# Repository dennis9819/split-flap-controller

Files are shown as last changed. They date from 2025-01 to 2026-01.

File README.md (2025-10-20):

# 3D Printable split flap display

Welcome to **split-flap-controller**, the firmware + hardware design for driving a modular, scalable split-flap display system.
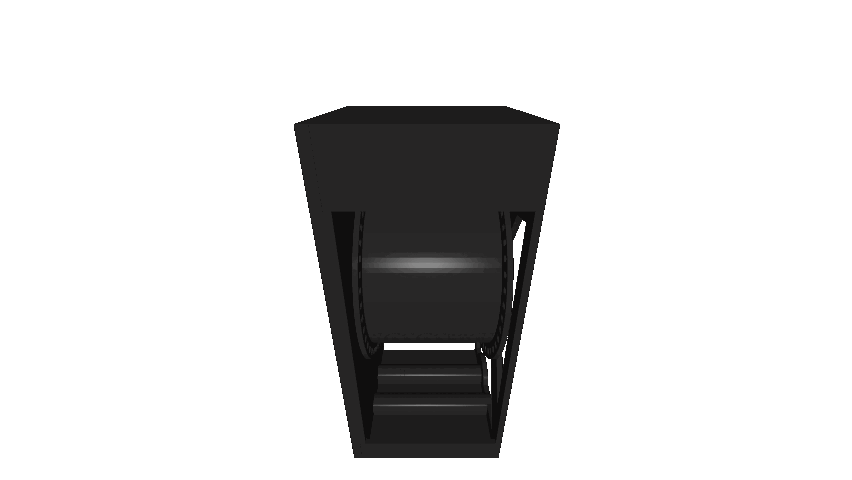
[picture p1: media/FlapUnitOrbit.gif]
Orbit View of Flap Unit


Development of this project began in 2024 with the goal of creating a robust, DIY split-flap display that anyone can build and customize themselves. Inspired by the iconic Frankfurt Airport display, this project aims to recreate the nostalgic mechanical aesthetic and characteristic flipping sound that made those displays so memorable.

__Ongoing Project! This repository is not final.__

## Project goals
- **Modularity** – Each flap module is independent and addressable, allowing for scalable display sizes.  
- **DIY-Friendly Design** – Open schematics, PCBs, and firmware make it accessible for makers and hobbyists.  
- **Robust Firmware** – Written in C, with features like error handling, EEPROM-stored calibration, and motor homing logic.  
- **Authentic Aesthetic** – Recreates the distinctive motion and sound of traditional airport-style displays.  
- **Modern Communication** – Supports RS-485 half-duplex at 57600 baud with WebSocket integration for control from a host system.  
- **Open for Extension** – Designed to support other MCUs, motor drivers, or mechanical formats.

## Features

### Hardware
- SMD-based controller board (Atmega8 MCU)  
- Modular RS-485 communication chain 
- Integrated motor driver and position sensor handling
- Modules connect to a single backplane
- Hall-effect sensor homing
- Robust error handling
  - detects homing faults, stuck drums, overcurrent and bus errors
  - activates a failSafe condition on critical fault
  - can be reset via RS485 in most conditions
  - checks validity of each packet via checksum

### Firmware
- Lightweight communication protocol with checksum and addressing  
- Fault detection (homing failure, overcurrent, invalid position)  
- Persistent settings stored in EEPROM  
- CRC check of each message

### Software
- WebSocket-based control server  
- Modular architecture for future GUI or API integrations  
- Easily portable to other platforms and MCUs
- Nginx Webserver allows you to controll the display with your smartphone
- very fast and written in plan c. I'm using libjson and libws for JSON handling and the WebSocket server

## CAD
This display is designed in **Fusion360**. All schematics and boards are designed in **KiCAD 9**.

Most parts can be 3d printed. The modular backpanel needs to be fabricated from sheetmetal. You can use suppliers like JLCPCB for manufacturing or design a different 3d printable solution.

If you want to generate custom flaps, you can find my flap generator here: [split-flap-generator](https://github.com/dennis9819/split-flap-generator)

## License

This project is open source and available under the [AGPL-3.0 License](LICENSE).

## Documentation
- [SFBus Protocol](software/pc_client/doc/sfbus-proto.md)
- [Websockets Protocol](software/pc_client/doc/api-doc.md)
- [BOM](cad/BOM_FlapUnit.md)
- Build guide wil follow soon!

## Power Consumption
Each Module pulls arround 110mA. This is roughly 1.4W of power. 
This can be reduced by turning off the motors in idle. 

---
## Credits
This is a 3D printable, expandable split flap display based on the original design of [David Königsmann](https://github.com/davidkingsman/split-flap).
This version uses his drum and flap design but completly redesigns the rest of the system.

The firmware as well as the Server is completly rewritten from scratch.

Feel free to checkout his more affordable and diy friendly design.

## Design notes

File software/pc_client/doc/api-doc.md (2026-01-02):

# Websockets Interface documentation
All requests and responses are sent as json objects.

## Request
Every request must conatin at least one value: `command`
```
{
   "command": "<command>"
}	
```
### Device manager commands

#### Save config `dm_save`
Saves config to ./flapconfig.json.

Request:
```
{
   "command": "dm_load"
}	
```
Response:
```
{
   "ack": true
}	
```
#### Load config `dm_load`
Loads config from ./flapconfig.json.

Request:
```
{
   "command": "dm_load"
}	
```
Response:
```
{
   "ack": true
}	
```
#### Dump config `dm_dump`
Dumps current config to socket.

Request:
```
{
   "command": "dm_dump"
}	
```
Response:
```
{
   "devices_all": <registered device count>
   "devices_online": <online device count>,
   "devices": <array of all devices>,
   "map": <2D array of device locations>
}	
```

#### Describe single device `dm_describe`
Gets all information for specified device id.

Request:
```
{
   "command": "dm_describe",
   "id": <device id>
}	
```
Response:
```
{
   ...
}	
```
#### Register new device `dm_register`
Register device, assign new id and assign a location.
```
{
   "command": "dm_describe",
   "address": <device bus address>,
   "x": <x position on screen>,
   "y": <y position on screen>,
}	
```
Response:
```
{
   "id": <assigned device id>
}	
```

#### Remove device from config `dm_remove`
Removes device from config and frees location in screen

Request:
```
{
   "command": "dm_remove",
   "id": <device id>
}	
```
Response:
```
{
   "ack": true
}	
```

#### Remove device from config `dm_refresh`
Refresh device config

Request:
```
{
   "command": "dm_refresh"
}	
```
Response:
```
{
   "devices_online": <online device count>
}	
```

#### Print string `dm_print`
Print string at position (x,y)

Request:
```
{
   "command": "dm_describe",
   "string": <string to display>,
   "mode": <int: 0=full rotation/1=direct/2=sync>,
   "x": <int: x position on screen>,
   "y": <int: y position on screen>
}	
```
Response:
```
{
   "ack": true
}	
```

#### Display flap number `dm_print_single`
Print string at position (x,y)

Request:
```
{
   "command": "dm_print_single",
   "flap": <int: flap to display>,
   "full": <boolean: full rotation of drum/recalibration>,
   "x": <int: x position on screen>,
   "y": <int: y position on screen>
}	
```
Response:
```
{
   "ack": true
}	
```

#### Display clear `dm_clear`
Clears all flaps.

Request:
```
{
   "command": "dm_clear"
}	
```
Response:
```
{
   "ack": true
}	
```

### Device raw commands

#### Ping module `dr_ping`
Checks if a module reponds on the given address.

Request:
```
{
   "command": "dr_ping",
   "address": <address>
}	
```
Response:
```
{
   "success": <boolean: if device reponded 'true', else 'false'>
}	
```

#### Set module address `dr_setaddress`
Changes the hardware address of an module.

Request:
```
{
   "command": "dr_setaddress",
   "address": <address>,
   "newaddress": <new address>
}	
```
Response:
```
{
   "success": <boolean: if success 'true', else 'false'>
}	
```

#### Set module offset calibration `dr_setcalibration`
Sets the offset calibration for an module.

Request:
```
{
   "command": "dr_setcalibration",
   "address": <address>,
   "calibration": <calibration value (default: 1800)>
}	
```
Response:
```
{
   "success": <boolean: if success 'true', else 'false'>
}	
```

#### Reset module `dr_reset`
Resets the controller of an module

Request:
```
{
   "command": "dr_reset",
   "address": <address>
}	
```
Response:
```
{
   "ack": true
}	
```

#### Display flap `dr_display`
Sets the module to the specified flap directly or with recalibration.

Request:
```
{
   "command": "dr_display",
   "address": <address>,
   "flap": <flap-number>,
   ("full": <boolean: full rotation of drum/recalibration>)

}	
```
Response:
```
{
   "ack": true
}	
```

#### Power module on/off `dr_power`
Sets the power-state for the motor of the given module.

Request:
```
{
   "command": "dr_power",
   "address": <address>,
   "power": <boolean: power on>

}	
```
Response:
```
{
   "ack": true
}	
```

## Responses
### Error:
```
{
   "error": "<error name>",
   "detail": "<more detailed error message>"
}	
```
The following responses are valid:
- `parsing error`: the json request is malformated and cannot be parsed
- `format error`: the json object is missing required fields. Check details for more information.
- `internal error`: an internal error occured. This should not happen. Chaeck server logs.

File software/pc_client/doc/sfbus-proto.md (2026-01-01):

# SplitflapBus protocol
## Terminology
* *main controller interface*: RS485 interface, connected to the mangment pc. Serves as bus master.
* *node*: Participant on bus. Can be a controller interface or an flap controller.
* *flap controller*: Microcontroller located in each flap module that processes requests and drives motor.

## Protocol implementation
The SF-Bus is an RS485 based protocol. It has a singular master node and up to 32 client *nodes* per interface.  It can address up to 65536 *devices*.

The communication is always initiated by the *main controller interface*, serving as the bus *master*.
The start of a new communication is signaled by sending the start byte `0x2B` to the bus, followed by the protocol version (8-bit) and frame length (8-Bit). Each connected *node* now captures the entire packet, even if the adress does not match its own. This reduces the risk of the *node* falsely identifying payload data as a start byte if it contains the value `0x2B`.

After the transmission of the payload length, the receiver *node* counts the remaining packages and terminates the transmission at 0 bytes remaining. The data is written to a buffer for further processing.

In protocol version 1.0, the receiving *node* expects the last byte to be `0x24`. If this is not the case, the transmission is marked as invalid and will not be processed further. The receiving *node* will not send any response.

In protocol version 2.0, the checksum of the payload is verified. If it does not match the payload, the transmission is marked as invalid and will not be processed further. The receiving *node* will not send any response.
No stop-byte is expected. Version 2.0 also requires a timeout-check in the receiving function. This allows the bus to support hot-plugging, to cancel incomplete or invalid packages and reliably detect the start of a new transmission.

The communication is typically unidirectional. Lost transmissions are not detectable. The *flap controller* NEVER initiates a communication to the *main controller interface*. *node* to *master* communication only occures in response to specific commands. This is specified in the command / payload documentation.

## Packet format (2.0)
```
+---------------------------------+----------------------------------------+
| Header                          | Frame                                  |
+------------+-----------+--------+----------+-----------------+-----------+
| Start-Byte | Protocol- | Frame- | Receiver | Payload         | Checksum  |
|            | Version   | Length | Address  |                 |           |
| 0x2B       | 0x01      | 1 byte | 2 bytes  | framelength - 4 | 2 bytes   |
+------------+-----------+--------+----------+-----------------+-----------+
 The frame length includes the 16-bit address and 16 bit checksum.
 Therefor, the payload is framelegth - 4.

 Checksum is based on MODBUS CRC algorithm. Check implementation in sfbus.c
 Checksum is only created for the payload, not the entire frame or packet.
```

More infromation regarding the crc algorithm: https://ctlsys.com/support/how_to_compute_the_modbus_rtu_message_crc/

## Payload format (Protocol Version 1.0 + 2.0)
The first byte of the payload is the command. This tells the controller
what to do or what data to expect next.

```
+----------+----------------+
| Command  | Payload        |
| Byte     |                |
| 1 Byte   | framelegth - 4 |
+----------+----------------+
```

### Ping
Check if a module is present under this device id
- Payload: `0xFE`
- Expected response: `0xFF`

### Reset
Resets the device controller. Should be done after address or calibration change.

Can also be done to clear error flags
- Paylad `0x30`
- Expects no response.

### Motor power on
- Paylad `0x21`
- Expects no response.

### Motor power off
- Paylad `0x20`
- Expects no response.

### Display flap
- Paylad `0x10 <1 byte: flap id>`
- Expects no response.

### Display flap with full rotation
- Paylad `0x11 <1 byte: flap id>`
- Expects no response.

### Read EEPROM
Read address and calibration configuration from internal non-volatile memory.
- Payload `0xF0`
- Response is `0xAA` followed by content of EEPROM (5 bytes). See mapping below.

### Write EEPROM
Write address and calibration configuration to internal non-volatile memory.
- Payload `0xF1 <5 bytes of eeprom content>`
- Response is `0xAA` followed by new content of EEPROM (5 bytes). See mapping below.

### Get controller status
- Payload `0xF8`
- Response is 7 bytes long.
```
+--------+------------+------------+
| Byte 0 | Byte 1 - 2 | Byte 3 - 6 |
| 8-Bit  | 16-Bit     | 32-Bit     |
| Status | Voltage    | Rotations  |
+--------+------------+------------+
  |         |            |
  |         |            +-> uint32 counter of total rotations
  |         |
  |         +-> uint16 raw ADC readings.
  |             double __voltage = ((double)_voltage / 1024) * 55;
  |
  +->   Bit 0:  delta too big. Sensed position not equal to expected position
        Bit 1:  no home found. Cannot sense home magnet.
        Bit 2:  fuse blown
        Bit 4:  device powered down. Can be changed by sending: 0x21
        Bit 5:  failsafe active. Device failed cirtically and stopped operation.
                can be recovered with reset: 0x30
        Bit 6:  device busy. Device is currently moving to the next flap position

```

### Get controller firmware version
- Payload `0xF9`
- Response is 3 bytes long: `<major> <minor> <patch>`.

## EEPROM format
```
+------------+------------+--------+
| Byte 0 - 1 | Byte 2 - 5 | Byte 6 |
| 16-Bit     | 32-Bit     | 8-Bit  |
| Address    | Rotations  | Okay   |
+------------+------------+--------+
  |             |           |
  |             |           +-> do not change
  |             |
  |             +-> uint32 counter of total rotations
  |
  +-> uint16 device address
```

## Address management
* Address `0x0000` is reserved for new devices. These devices needs a new address before it can be used. Use the `Write EEPROM` method to change it.
* Address `0xFFFF` is reserved for the bus *master* and must never be used by another node. Each *node* to *master* response package must be sent to this address.
* All remaining addresses can be freely assigned.

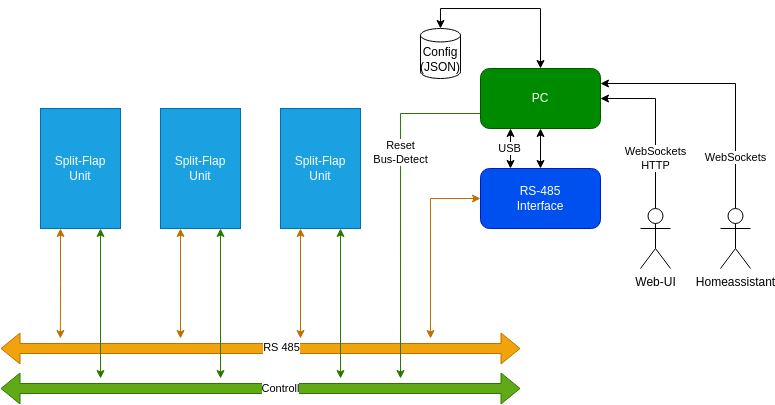
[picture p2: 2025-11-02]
media/SplitFlap-Doc-Overview.drawio.png

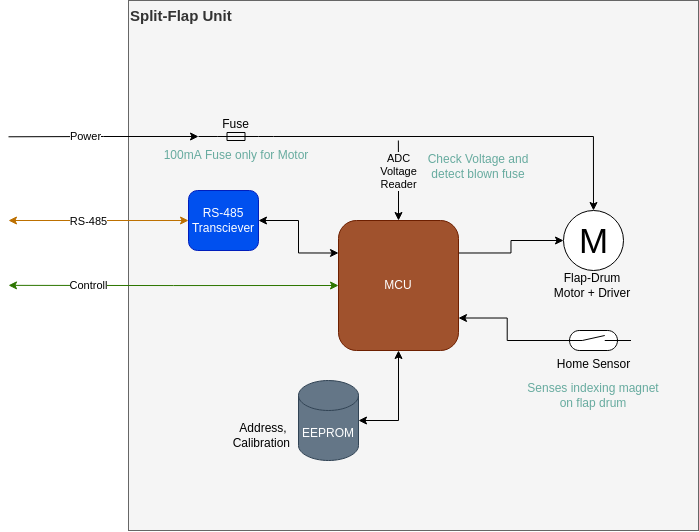
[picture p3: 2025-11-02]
media/SplitFlap-Doc-Module.drawio.png

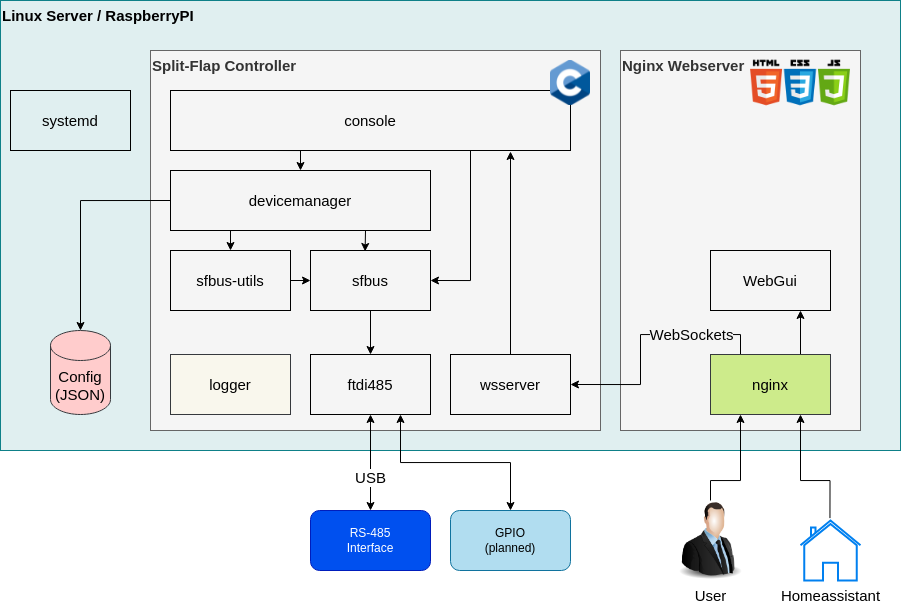
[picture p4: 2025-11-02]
media/SplitFlap-Doc-Controller-SW.drawio.png

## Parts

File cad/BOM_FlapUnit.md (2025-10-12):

# Bill of Material for 1U/2U Flap Unit

## 3D Printed Parts 
| part-number | part | file | amount | notes |
| --- | ---- | ---- | --- | ----- |
| FU-001 | Unit Frame Base | STL Unit/splitflap-unit-base.stl | 1 | common for all units |
| FU-002 | Unit Frame Cover 1U | STL Unit/splitflap-cover-1u.stl  | 1 | only for 1U wide unit|
| FU-003 | Unit Frame Cover 2U | STL Unit/splitflap-cover-2u.stl  | 1 | only for 2U wide unit|
| FU-004 | Unit Drum Core | STL Unit/splitflap-drum-core.stl | 1 | common for all units |
| FU-005 | Unit Drum Core 1U | STL Unit/splitflap-drum-outer-1u.stl | 1 | only for 1U wide unit|
| FU-006 | Unit Drum Core 2U | STL Unit/splitflap-drum-outer-2u.stl | 1 | only for 2U wide unit|
| FU-007 | Flaps | ... | 45 | |
- 49 Individual Parts per module

## Hardware

| part-number | part | amount | notes |
| --- | ---- | --- | ----- |
| FU-011 | Ball Bearing 684ZZ (9 x 4 x 4mm) | 1 | |
| FU-012 | Stepper 28BYJ-48 DC 12V | 1 |  **!! Use 12V Variant. NOT 5V !!**|
| FU-013 | Heat insert M3 x 3mm | 3 | |
| FU-014 | Heat insert M3 x 5mm | 4 | |
| FU-015 | M3x5 Screw DIN 912 | 3 | |
| FU-016 | M3x12 Screw DIN 912 | 2 | |
| FU-017 | M3x8 Screw DIN EN ISO 10642 | 2 | |
| FU-018 | Magnet round d=2mm | 1 | |
- 17 Individual Parts per module

## Electronics
| part-number | part | amount | notes |
| --- | ---- | --- | ----- |
| FU-031 | Module Controller PCB | 1 | |
| FU-032 | ATmega8A-A | 1 | |
| FU-033 | SN75176AP | 1 | |
| FU-034 | ULN2003 | 1 | Can be salvaged from the driver board that usually comes with the stepper motor |
| FU-035 | A1101xLH | 1 | SOT-23W variant! |
| FU-036 | 16,0000-HC49U-S Crystal | 1 |  |
| FU-037 | Capacitor 10u 35V (Radial_D6.3mm_P2.50mm) | 1 |  |
| FU-038 | Capacitor 10u 16V (1206) | 1 |  |
| FU-039 | Capacitor 22p (0805) | 2 |  |
| FU-040 | Capacitor 100n (0805) | 4 |  |
| FU-041 | Fuse 200mA (0805) | 1 |  |
| FU-042 | JST B5B-XH-A | 1 |  |
| FU-043 | Resistor 1k | 1 |  |
| FU-044 | Resistor 10k | 3 |  |
- 20 Individual Parts per module

## Summary:
Parts per module: 76 (mostly 3d printed)

# Bill of Material for 4Unit Backplane

## 3D Printed Parts 
| part-number | part | file | amount | notes |
| --- | ---- | ---- | --- | ----- |
| FP-001 | Upper Slot | STL Slot/splitflap-slot-upper.stl | 1 |  |
| FP-002 | Lower Slot | STL Slot/splitflap-slot-lower.stl | 1 |  |
- 2 Individual Parts per module

## Sheet metal
| part-number | part | file | amount | notes |
| --- | ---- | ---- | --- | ----- |
| FP-003 | Backplane | Sheet Metal/sheet-metal-backplate.dxf | 1 |  |
- 1 Individual Parts per module

## Hardware
| part-number | part | amount | notes |
| --- | ---- | --- | ----- |
| FP-011 | Heat insert M4 x 5mm | 4 | |
| FP-012 | Heat insert M3 x 5mm | 4 | |
| FP-013 | M3x5 Screw DIN 912 | 8 | |
| FP-014 | M4x10 Screw DIN 912 | 4 | |
| FP-015 | M3x5 Standoff | 8 | |
| FP-016 | M3 Nut | 4 | |
- 32 Individual Parts per module

## Electronics
| part-number | part | amount | notes |
| --- | ---- | --- | ----- |
| FP-031 | Backplane PCB | 1 | |
| FP-032 | PhoenixContact_MSTBA_2,5_2-G-5,08 | 2 | |
| FP-033 | Phoenix_MSTB:PhoenixContact_MSTBA_2,5_3-G-5,08 | 4 | |
| FP-034 | L7805 | 1 |  |
| FP-035 | 74AHCT1G125 | 1 | |
| FP-036 | 2x08 Edge Connector | 4 |  |
- 13 Individual Parts per module

## Summary:
Parts per assembly: 48 

# Bill of Material for Backplane connection bracket
## Sheet metal
| part-number | part | file | amount | notes |
| --- | ---- | ---- | --- | ----- |
| FC-001 | Bracket | sheet-metal-connector-middle.dxf | 1 |  |
- 1 Individual Parts per module

## Hardware
| part-number | part | amount | notes |
| --- | ---- | --- | ----- |
| FC-011 | M4x10 | 8 | |
| FC-012 | M4 Nut | 8 | |
- 16 Individual Parts per module

## Summary:
Parts per assembly: 17 

# Parts for full display (12x3)
- Display Units: 36 (2736 Parts)
- Backplane Units: 9 (432 Parts)
- Backplane Connectors: 12 (204 Parts)
- Sum: 3372 Individual Parts

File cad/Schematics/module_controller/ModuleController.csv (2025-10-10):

Reference | Value | Footprint | Datasheet | Qty | DNP
C1 | 10u 35V | Capacitor_THT:CP_Radial_D6.3mm_P2.50mm | ~ | 1
C2 | 10u 16V | Capacitor_SMD:C_1206_3216Metric | ~ | 1
C3,C4 | 22p | Capacitor_SMD:C_0805_2012Metric | ~ | 2
C5,C6,C7,C8 | 100n | Capacitor_SMD:C_0805_2012Metric | ~ | 4
F1 | RXEF010 | Capacitor_THT:C_Disc_D7.5mm_W2.5mm_P5.00mm | ~ | 1
H1,H2,H3 | MountingHole | MountingHole:MountingHole_3.2mm_M3 | ~ | 3
J1 | JST B5B-XH-A | Connector_JST:JST_XH_B5B-XH-A_1x05_P2.50mm_Vertical | ~ | 1
J6 | 2x08 Edge Connector | Dennis:Card Edge 16 power | ~ | 1
R1,R2,R4 | 10k | Resistor_SMD:R_0805_2012Metric | ~ | 3
R3 | 1k | Resistor_SMD:R_0805_2012Metric | ~ | 1
U1 | ULN2003 | Package_DIP:DIP-16_W7.62mm | http://www.ti.com/lit/ds/symlink/uln2003a.pdf | 1
U2 | A1101 | Dennis:UA A1101 | https://www.allegromicro.com/-/media/files/datasheets/a110x-datasheet.ashx | 1
U3 | SN75176AP | Package_DIP:DIP-8_W7.62mm | http://www.ti.com/lit/ds/symlink/sn75176a.pdf | 1
U4 | ATmega8A-A | Package_QFP:TQFP-32_7x7mm_P0.8mm | http://ww1.microchip.com/downloads/en/DeviceDoc/Microchip%208bit%20mcu%20AVR%20ATmega8A%20data%20sheet%2040001974A.pdf | 1
Y1 | 16,0000-HC49U-S | Crystal:Crystal_HC49-U_Vertical | ~ | 1

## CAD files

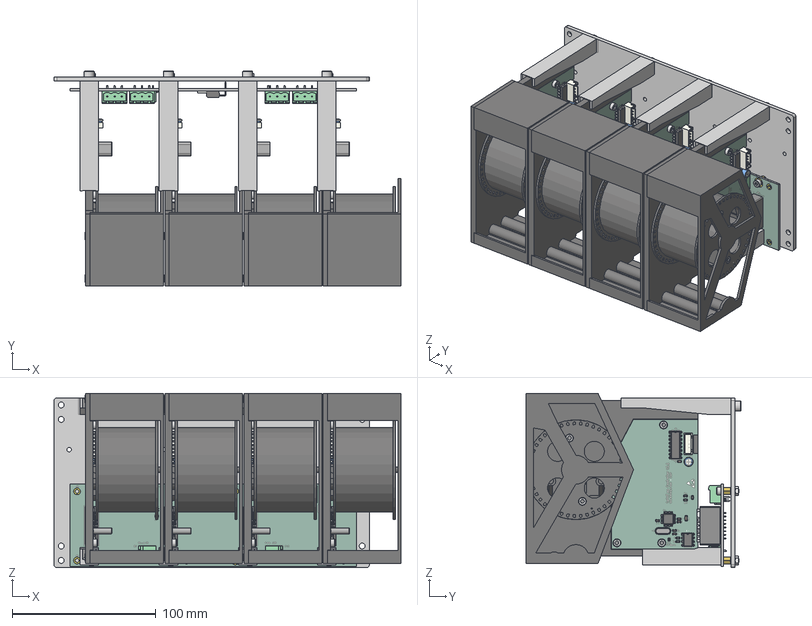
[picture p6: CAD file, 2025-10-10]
cad/STEP/SplitFlap Assembly.step
241.0 x 149.2 x 121.0 mm
Frame x 4
Cover 1U x 4
BigRotor x 4
MiniRotor x 4
DIN 912 - M3 x 0.5 x 8 Steel 4.6 Plain x 12
C_1206_3216Metric x 4
C_0805_2012Metric x 24
R_0805_2012Metric x 16
Crystal_HC49-U_Vertical x 4
TQFP-32_7x7mm_P0.8mm x 4
CP_Radial_D6.3mm_P2.50mm x 4
DIP-16_W7.62mm x 4
SOT-23W x 4
DIP-8_W7.62mm x 4
JST_XH_B5B-XH-A_1x05_P2.50mm_Vertical x 4
Fuse_0805_2012Metric x 4
ModuleController_copper x 4
ModuleController_pad x 4
ModuleController_via x 4
ModuleController_silkscreen x 4
ModuleController_soldermask x 4
ModuleController_PCB x 4
DIN 912 - M3 x 0.5 x 5 Steel 4.6 Plain x 16
DIN EN ISO 10642 - M3 x 8 Steel 8.8 Plain x 8
PhoenixContact_MSTBA_2,5_2-G-5,08_1x02_P5.08mm_Horizontal x 2
Card Edge Slot Connector casing x 4
EDGE_CONN_PIN x 64
PhoenixContact_MSTBA_2,5_3-G-5,08_1x03_P5.08mm_Horizontal x 4
TO-220-3_Horizontal_TabDown
SOT-353_SC-70-5
splitflap-backplane_copper
splitflap-backplane_silkscreen
splitflap-backplane_soldermask
splitflap-backplane_PCB
back-plate
M3_M_TO_F_5MM_STANDOFF x 8
DIN 934 - M3 x 0.5 Steel 6 Plain x 8
F1-B-M4-Heatfit x 4
DIN 912 - M4 x 0.7 x 8 Steel 4.6 Plain x 4

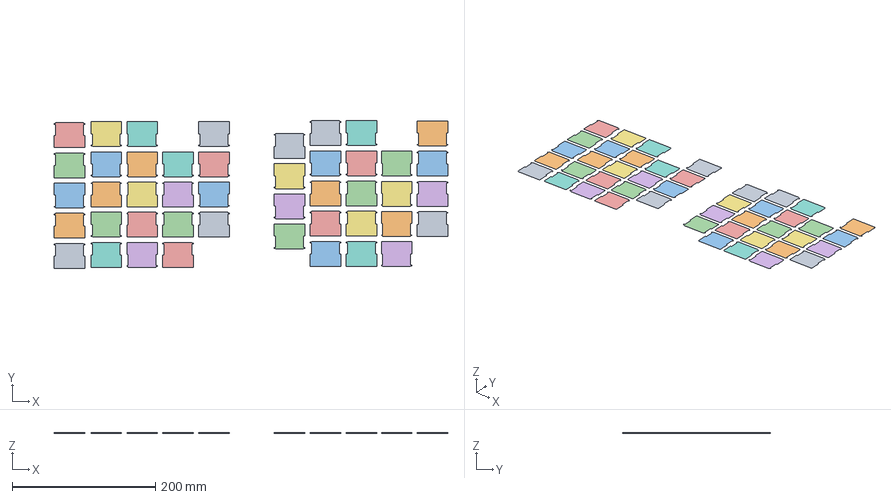
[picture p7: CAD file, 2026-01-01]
cad/Orca/SF_Flaps_V1.3mf
549.9 x 206.2 x 1.00 mm
Flap31.stl
Flap27.stl
Flap28.2.stl
Flap3.stl
Flap15.stl
Flap4.stl
Flap5.stl
Flap25.stl
Flap32.stl
Flap33.stl
Flap29.stl
Flap34.stl
Flap35.stl
Flap30.4.stl
Flap6.stl
Flap37.2.stl
Flap14.4.stl
Flap38.2.stl
Flap39.stl
Flap24.3.stl
Flap40.stl
Flap41.stl
Flap16.stl
Flap42.stl
Flap44.2.stl
Flap23.stl
Flap10.2.stl
Flap19.2.stl
Flap45.2.stl
Flap1.stl
Flap43.stl
Flap7.stl
Flap2.stl
Flap8.stl
Flap9.stl
Flap11.stl
Flap12.stl
Flap13.stl
Flap17.stl
Flap18.stl
Flap36.stl
Flap20.stl
Flap21.stl
Flap22.stl
Flap26.stl

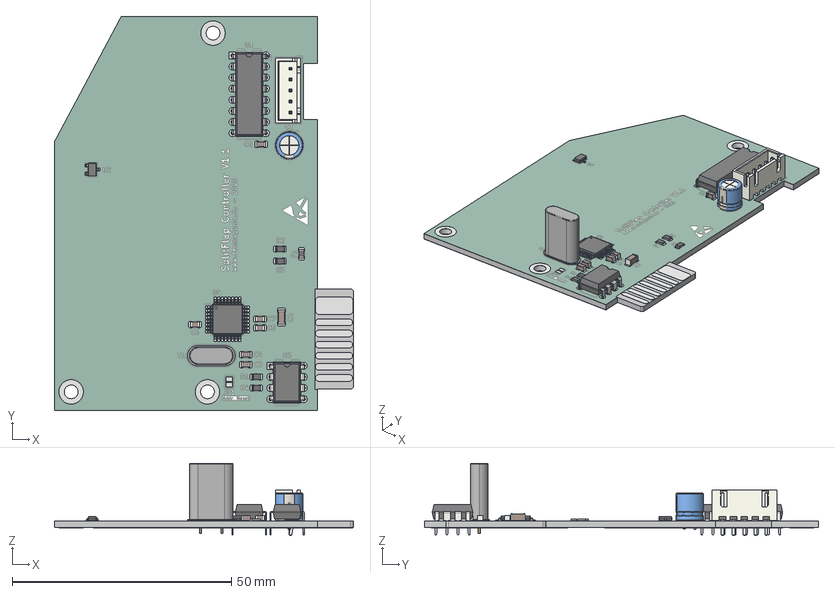
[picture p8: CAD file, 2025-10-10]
cad/Schematics/module_controller/ModuleController.step
68.3 x 90.0 x 16.5 mm
C_1206_3216Metric
C_0805_2012Metric x 6
R_0805_2012Metric x 4
Crystal_HC49-U_Vertical
TQFP-32_7x7mm_P0.8mm
CP_Radial_D6.3mm_P2.50mm
DIP-16_W7.62mm
SOT-23W
DIP-8_W7.62mm
JST_XH_B5B-XH-A_1x05_P2.50mm_Vertical
Fuse_0805_2012Metric
ModuleController_copper
ModuleController_pad
ModuleController_via
ModuleController_silkscreen
ModuleController_soldermask
ModuleController_PCB

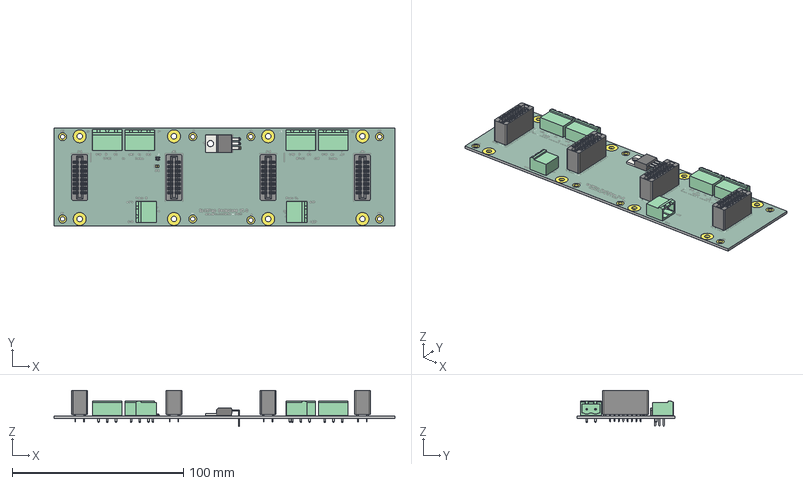
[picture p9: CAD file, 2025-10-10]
cad/Schematics/splitflap-backplane/splitflap-backplane.step
199.0 x 57.0 x 21.1 mm
PhoenixContact_MSTBA_2,5_2-G-5,08_1x02_P5.08mm_Horizontal x 2
Card Edge Slot Connector casing x 4
EDGE_CONN_PIN x 64
PhoenixContact_MSTBA_2,5_3-G-5,08_1x03_P5.08mm_Horizontal x 4
TO-220-3_Horizontal_TabDown
SOT-353_SC-70-5
splitflap-backplane_copper
splitflap-backplane_silkscreen
splitflap-backplane_soldermask
splitflap-backplane_PCB

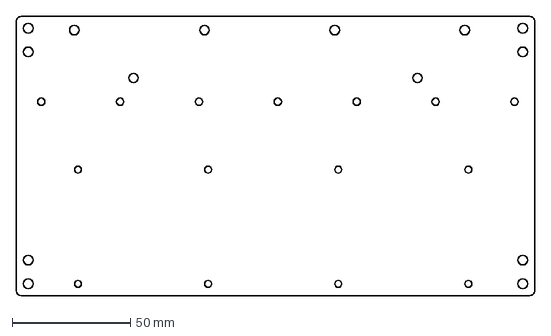
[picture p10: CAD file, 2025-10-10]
cad/Sheet Metal/sheet-metal-backplate.dxf
219.0 x 117.9 mm

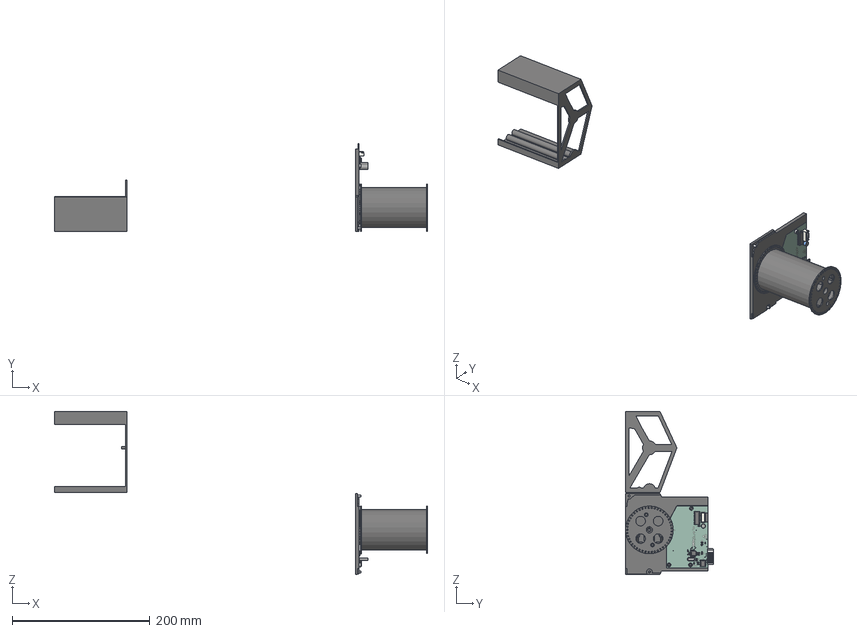
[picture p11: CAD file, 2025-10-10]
cad/STEP/SplitFlap Unit 2U.step
541.2 x 127.5 x 237.1 mm
Frame
Cover 2U
MiniRotor
BigRotor
C_1206_3216Metric
C_0805_2012Metric x 6
R_0805_2012Metric x 4
Crystal_HC49-U_Vertical
TQFP-32_7x7mm_P0.8mm
CP_Radial_D6.3mm_P2.50mm
DIP-16_W7.62mm
SOT-23W
DIP-8_W7.62mm
JST_XH_B5B-XH-A_1x05_P2.50mm_Vertical
Fuse_0805_2012Metric
ModuleController_copper
ModuleController_pad
ModuleController_via
ModuleController_silkscreen
ModuleController_soldermask
ModuleController_PCB
DIN 912 - M3 x 0.5 x 5 Steel 4.6 Plain x 3
DIN EN ISO 10642 - M3 x 8 Steel 8.8 Plain x 2

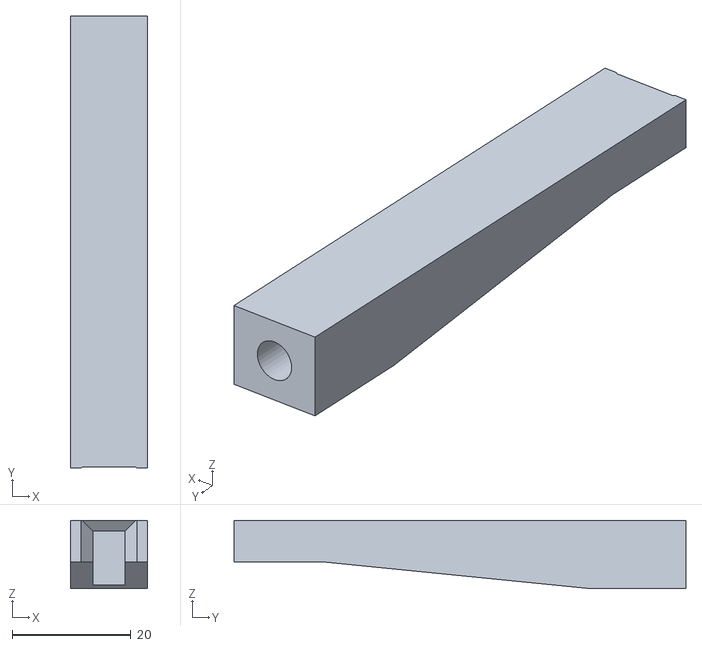
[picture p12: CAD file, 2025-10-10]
cad/STL Slot/splitflap-slot-upper.stl
13.0 x 76.2 x 11.5

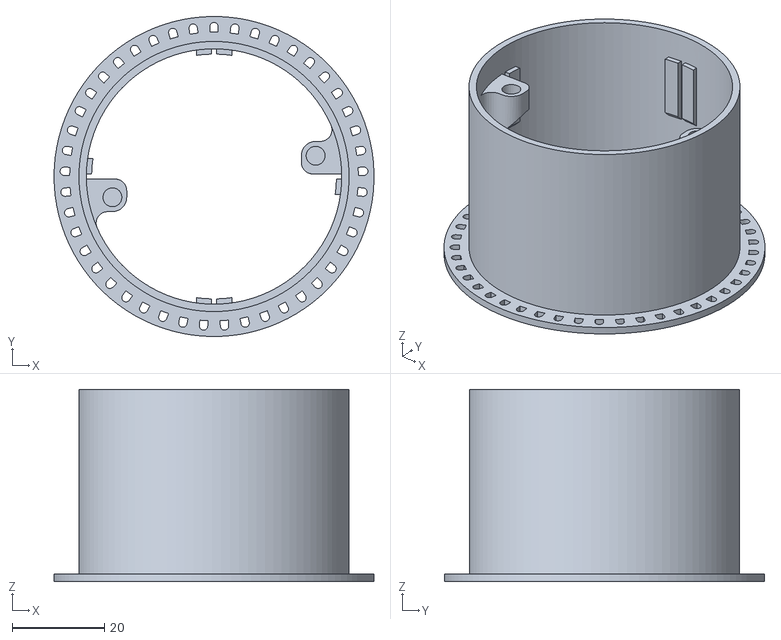
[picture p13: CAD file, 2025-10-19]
cad/STL Unit/splitflap-drum-outer-1u.stl
69.3 x 69.3 x 41.6

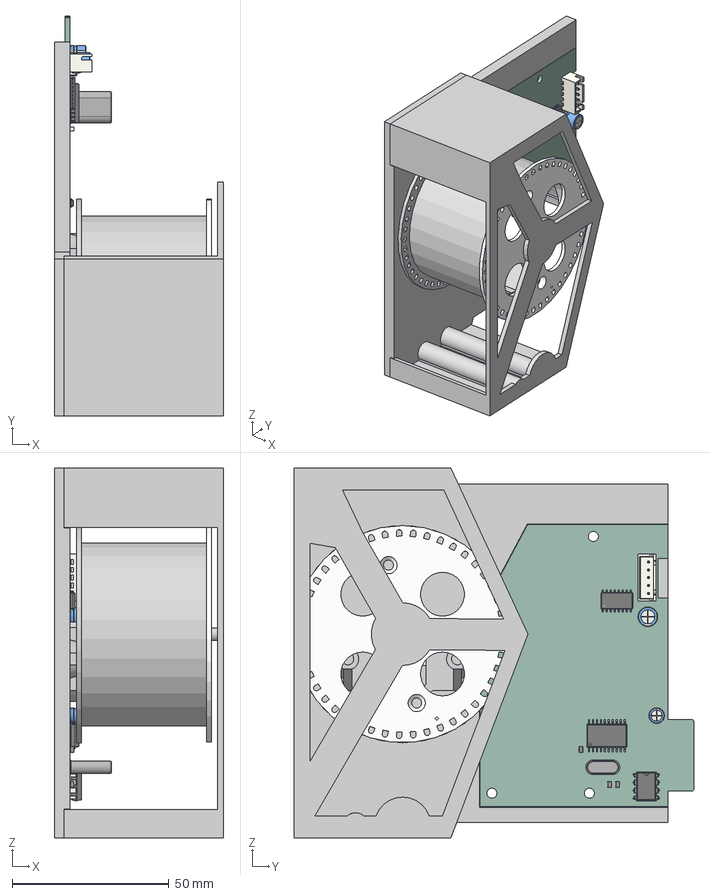
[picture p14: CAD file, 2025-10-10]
cad/Schematics/module_controller/Module.step
54.0 x 127.5 x 118.1 mm
Frame
MiniRotor
BigRotor
Cover
ModuleController PCB

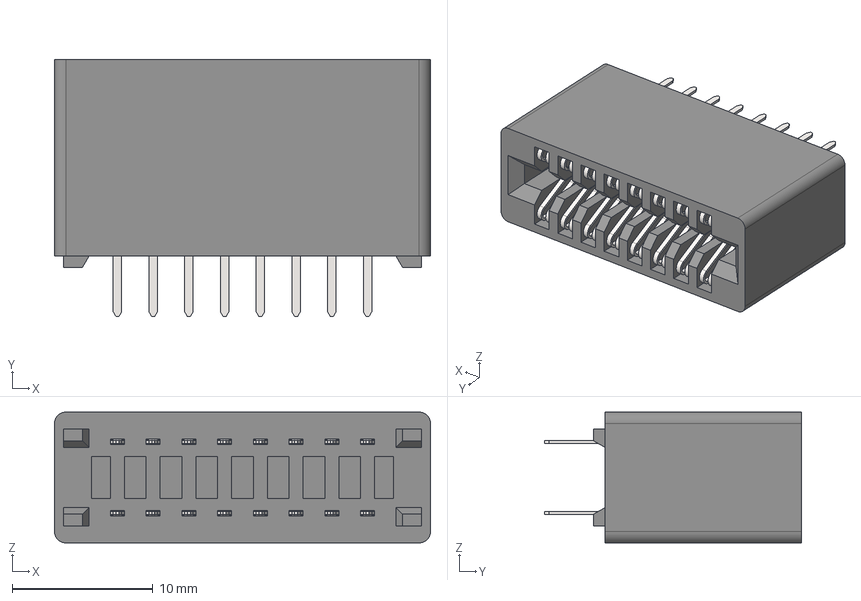
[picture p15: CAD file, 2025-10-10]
cad/Schematics/splitflap-backplane/edge-connector-16pin.step
26.7 x 18.3 x 9.30 mm
Card Edge Slot Connector casing
EDGE_CONN_PIN x 16

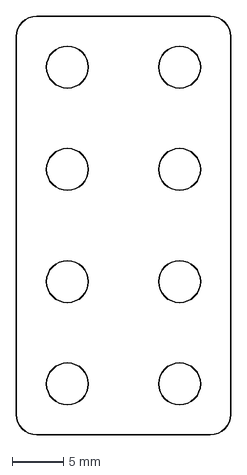
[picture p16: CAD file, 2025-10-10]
cad/Sheet Metal/sheet-metal-connector-middle.dxf
21.0 x 41.0 mm

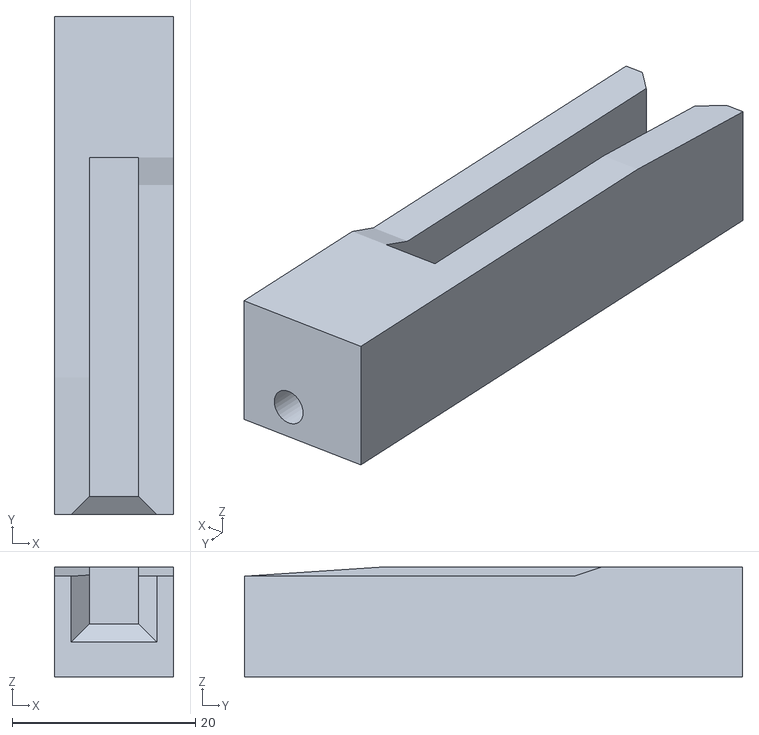
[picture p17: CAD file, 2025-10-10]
cad/STL Slot/splitflap-slot-lower.stl
13.0 x 54.4 x 12.0

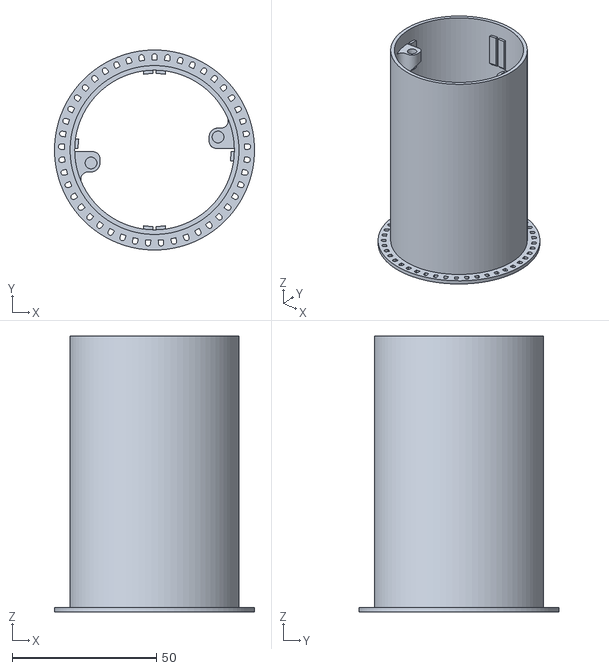
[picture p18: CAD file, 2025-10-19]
cad/STL Unit/splitflap-drum-outer-2u.stl
69.3 x 69.3 x 95.6

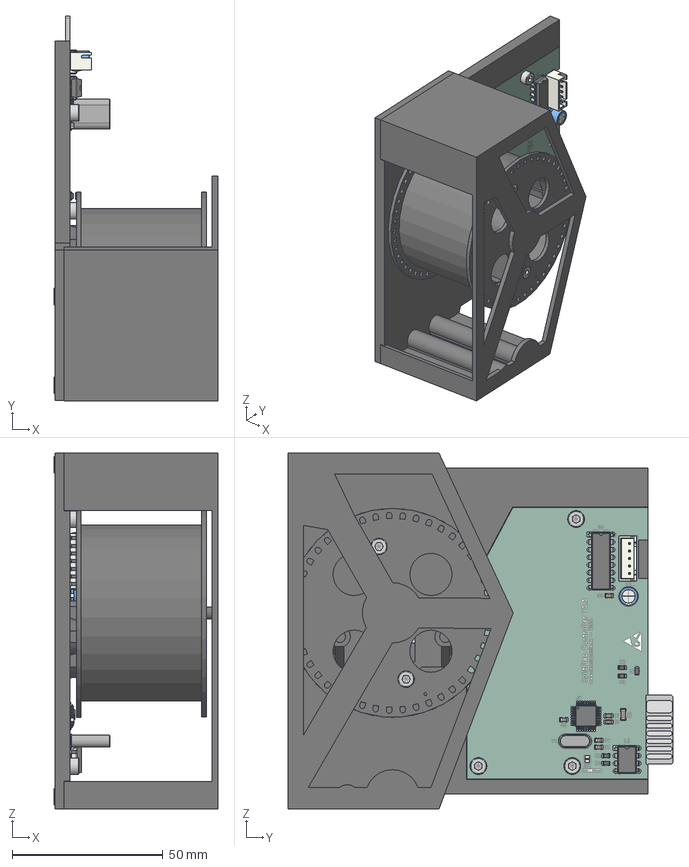
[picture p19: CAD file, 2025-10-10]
cad/STEP/SplitFlap Unit 1U.step
54.4 x 127.5 x 118.1 mm
Frame
Cover 1U
BigRotor
MiniRotor
DIN 912 - M3 x 0.5 x 8 Steel 4.6 Plain x 2
C_1206_3216Metric
C_0805_2012Metric x 6
R_0805_2012Metric x 4
Crystal_HC49-U_Vertical
TQFP-32_7x7mm_P0.8mm
CP_Radial_D6.3mm_P2.50mm
DIP-16_W7.62mm
SOT-23W
DIP-8_W7.62mm
JST_XH_B5B-XH-A_1x05_P2.50mm_Vertical
Fuse_0805_2012Metric
ModuleController_copper
ModuleController_pad
ModuleController_via
ModuleController_silkscreen
ModuleController_soldermask
ModuleController_PCB
DIN 912 - M3 x 0.5 x 5 Steel 4.6 Plain x 3
DIN EN ISO 10642 - M3 x 8 Steel 8.8 Plain x 2

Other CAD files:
cad/STL Unit/splitflap-cover-2u.stl
cad/STL Unit/splitflap-unit-base.stl
cad/STL Unit/splitflap-cover-1u.stl
cad/STL Unit/splitflap-drum-core.stl

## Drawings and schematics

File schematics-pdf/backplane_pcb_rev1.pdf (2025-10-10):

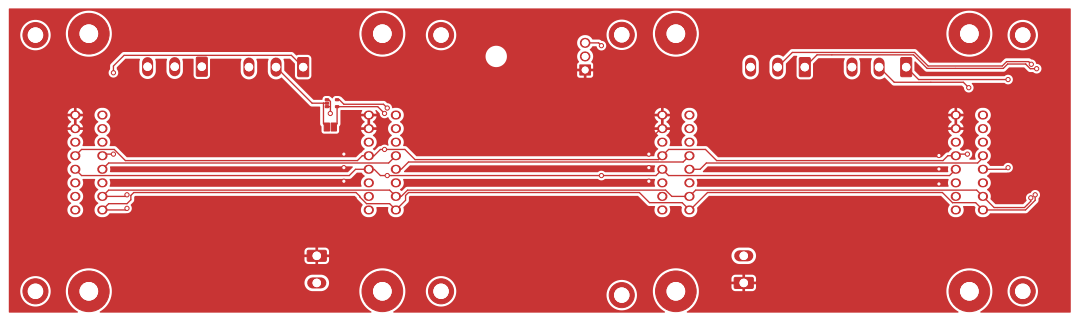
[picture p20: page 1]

File: splitflap-backplane.kicad_pcb Sheet: Dennis Gunia

Id: 1/7 Title: SplitFlap Display Module Backplane V1.1

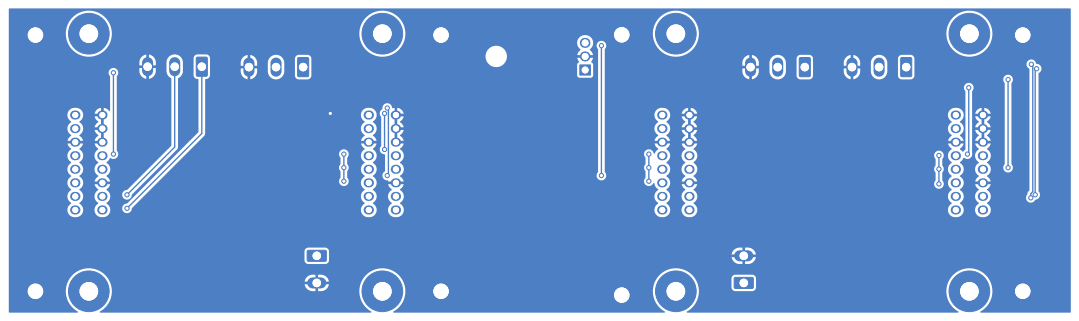
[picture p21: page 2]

File: splitflap-backplane.kicad_pcb Sheet: Dennis Gunia

Id: 2/7 Title: SplitFlap Display Module Backplane V1.1

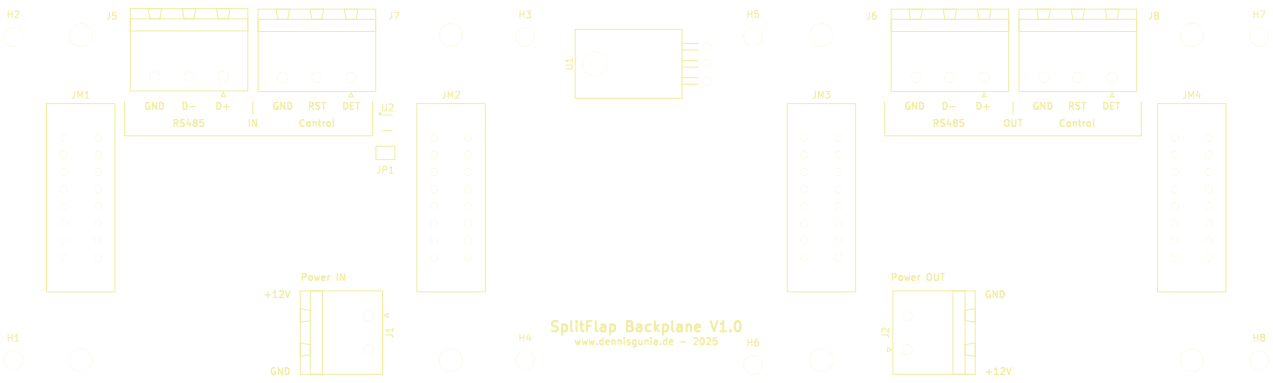
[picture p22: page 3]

File: splitflap-backplane.kicad_pcb Sheet: Dennis Gunia

Id: 3/7 Title: SplitFlap Display Module Backplane V1.1

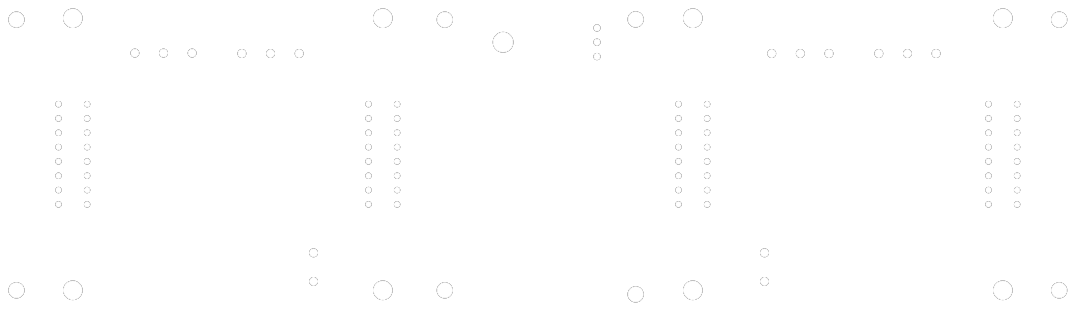
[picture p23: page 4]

File: splitflap-backplane.kicad_pcb Sheet: Dennis Gunia

Id: 4/7 Title: SplitFlap Display Module Backplane V1.1

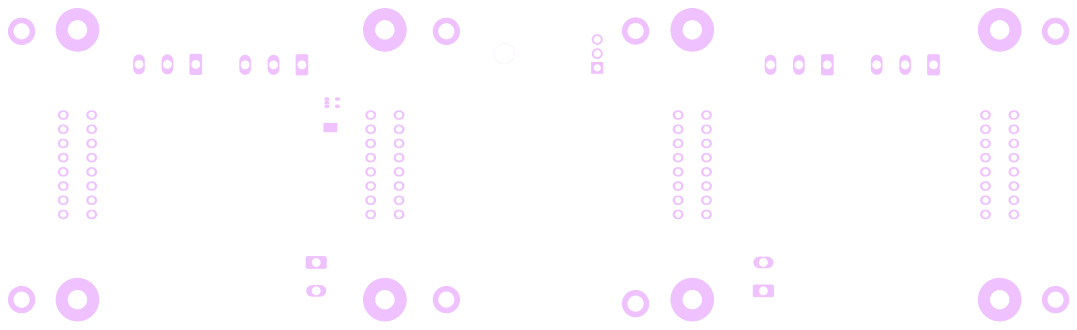
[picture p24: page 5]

File: splitflap-backplane.kicad_pcb Sheet: Dennis Gunia

Id: 5/7 Title: SplitFlap Display Module Backplane V1.1

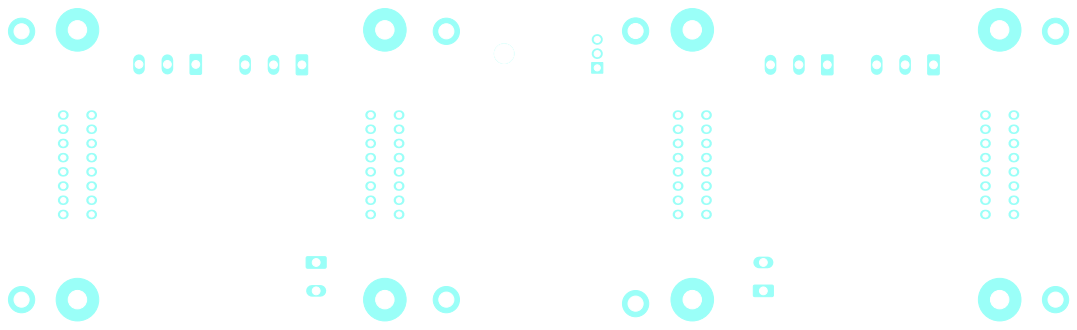
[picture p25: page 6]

File: splitflap-backplane.kicad_pcb Sheet: Dennis Gunia

Id: 6/7 Title: SplitFlap Display Module Backplane V1.1

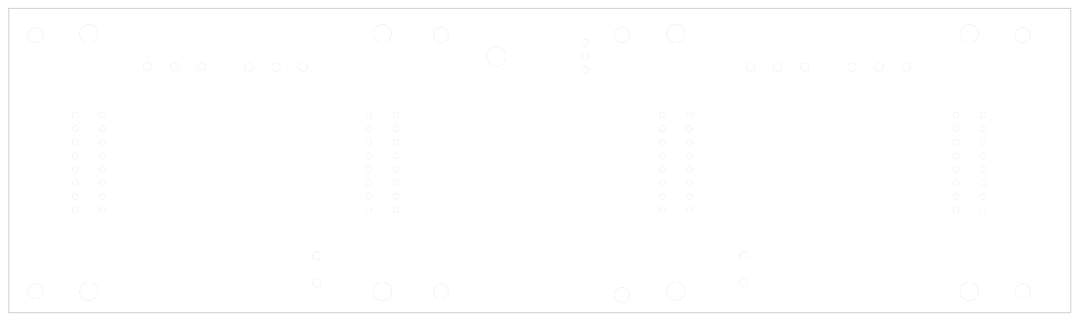
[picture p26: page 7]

File: splitflap-backplane.kicad_pcb Sheet: Dennis Gunia

Id: 7/7 Title: SplitFlap Display Module Backplane V1.1

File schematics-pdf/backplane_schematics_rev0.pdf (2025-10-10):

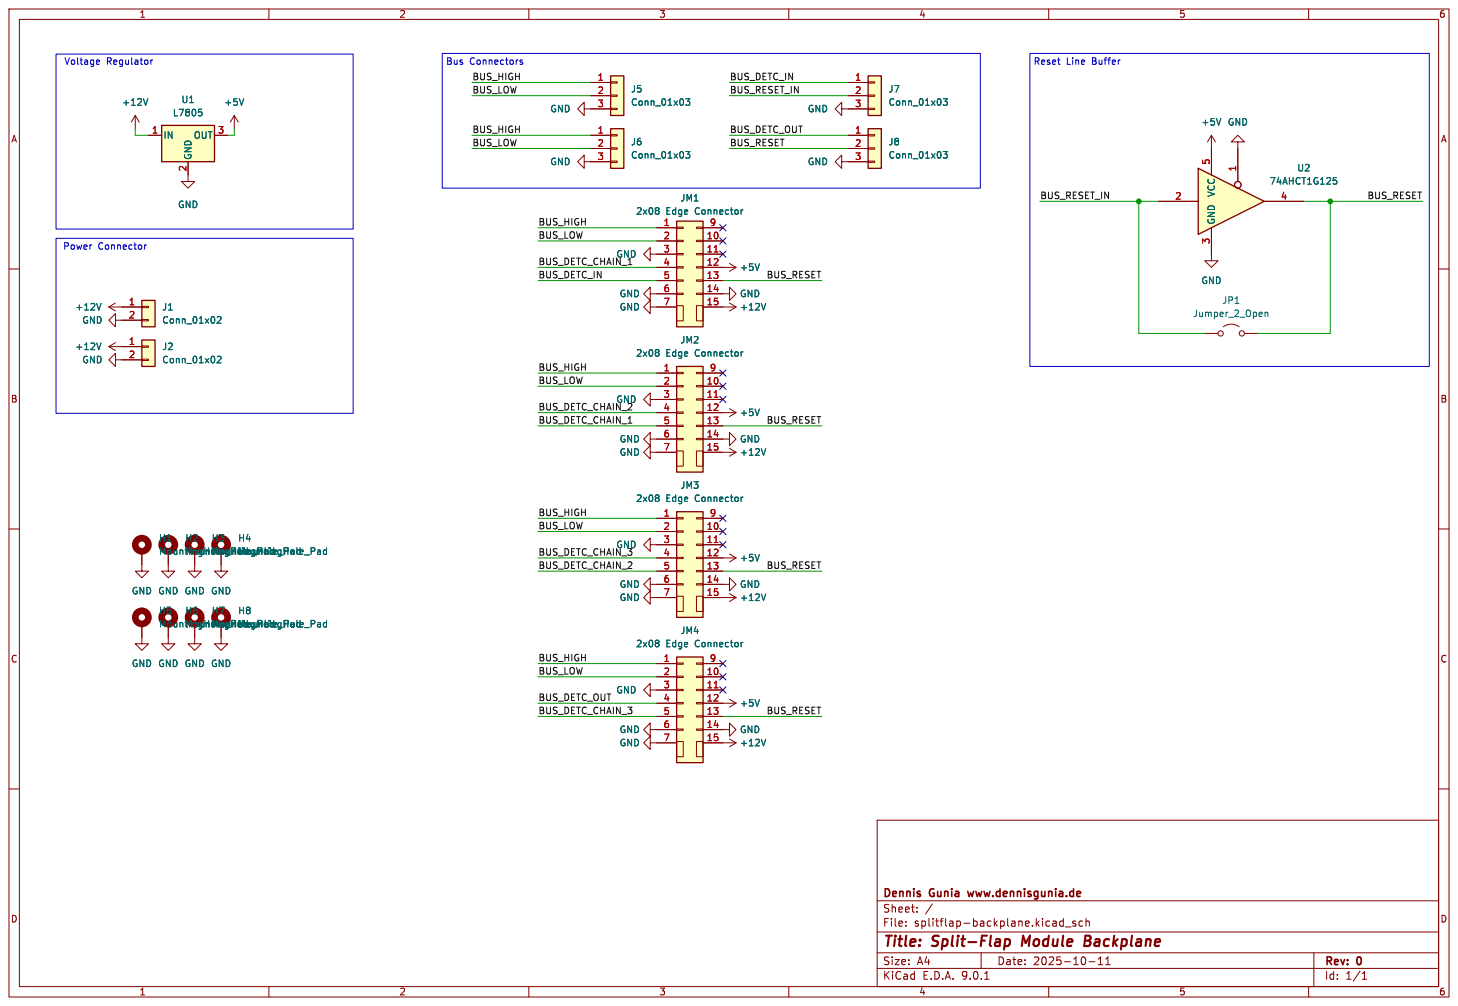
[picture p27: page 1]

File: splitflap-backplane.kicad_sch Sheet: / Dennis Gunia www.dennisgunia.de

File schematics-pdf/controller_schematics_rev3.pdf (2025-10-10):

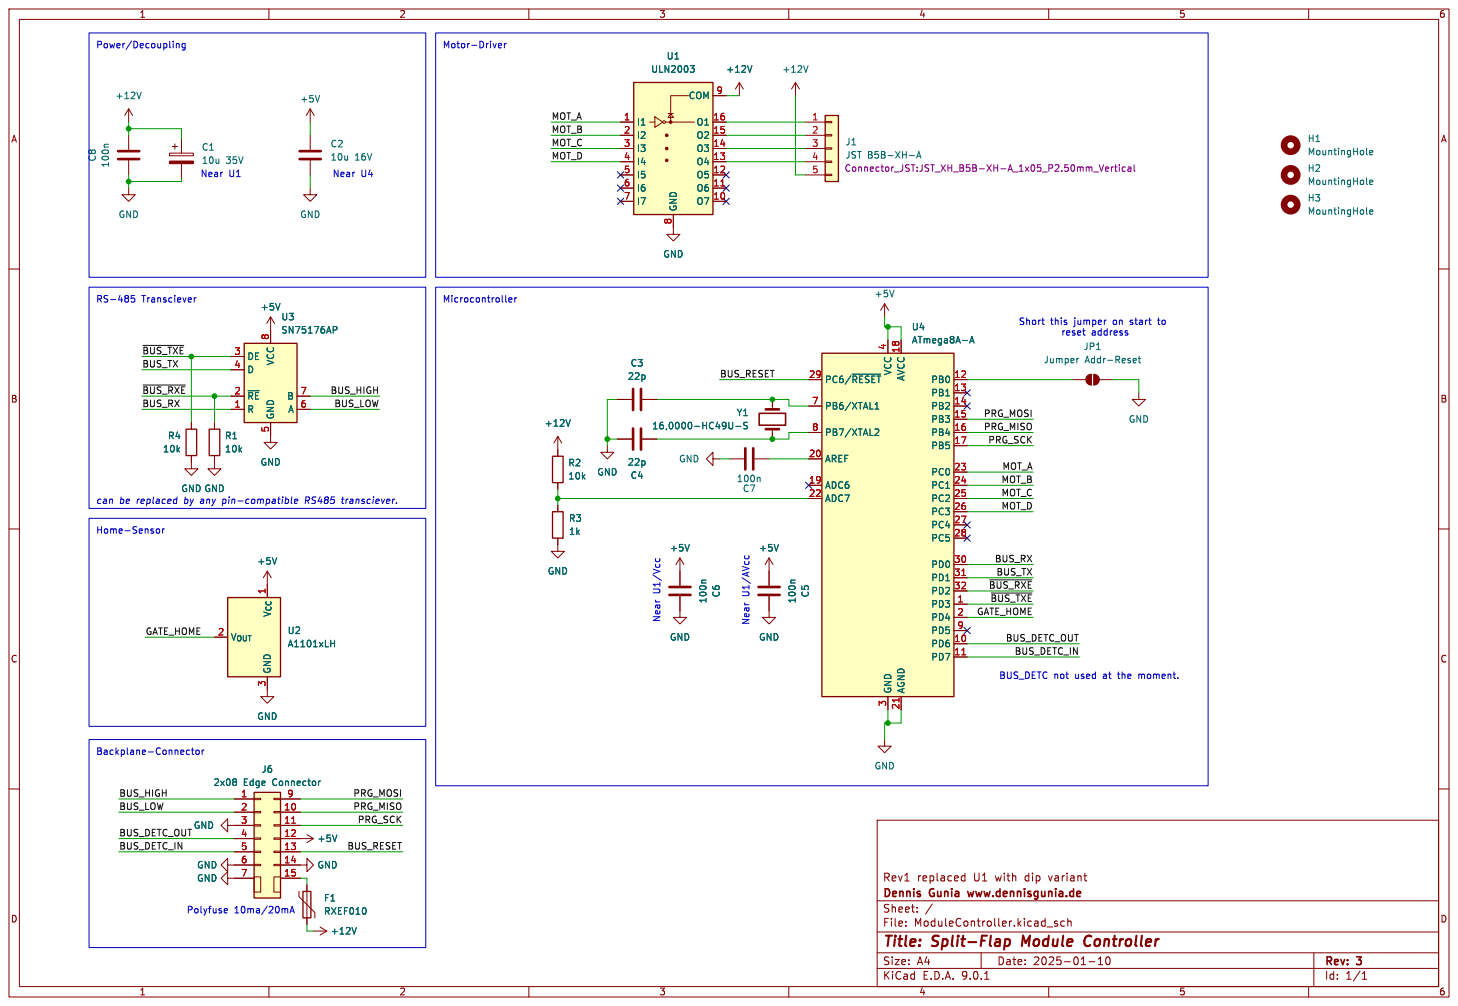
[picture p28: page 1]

BUS_DETC not used at the moment. Near U1/Vcc

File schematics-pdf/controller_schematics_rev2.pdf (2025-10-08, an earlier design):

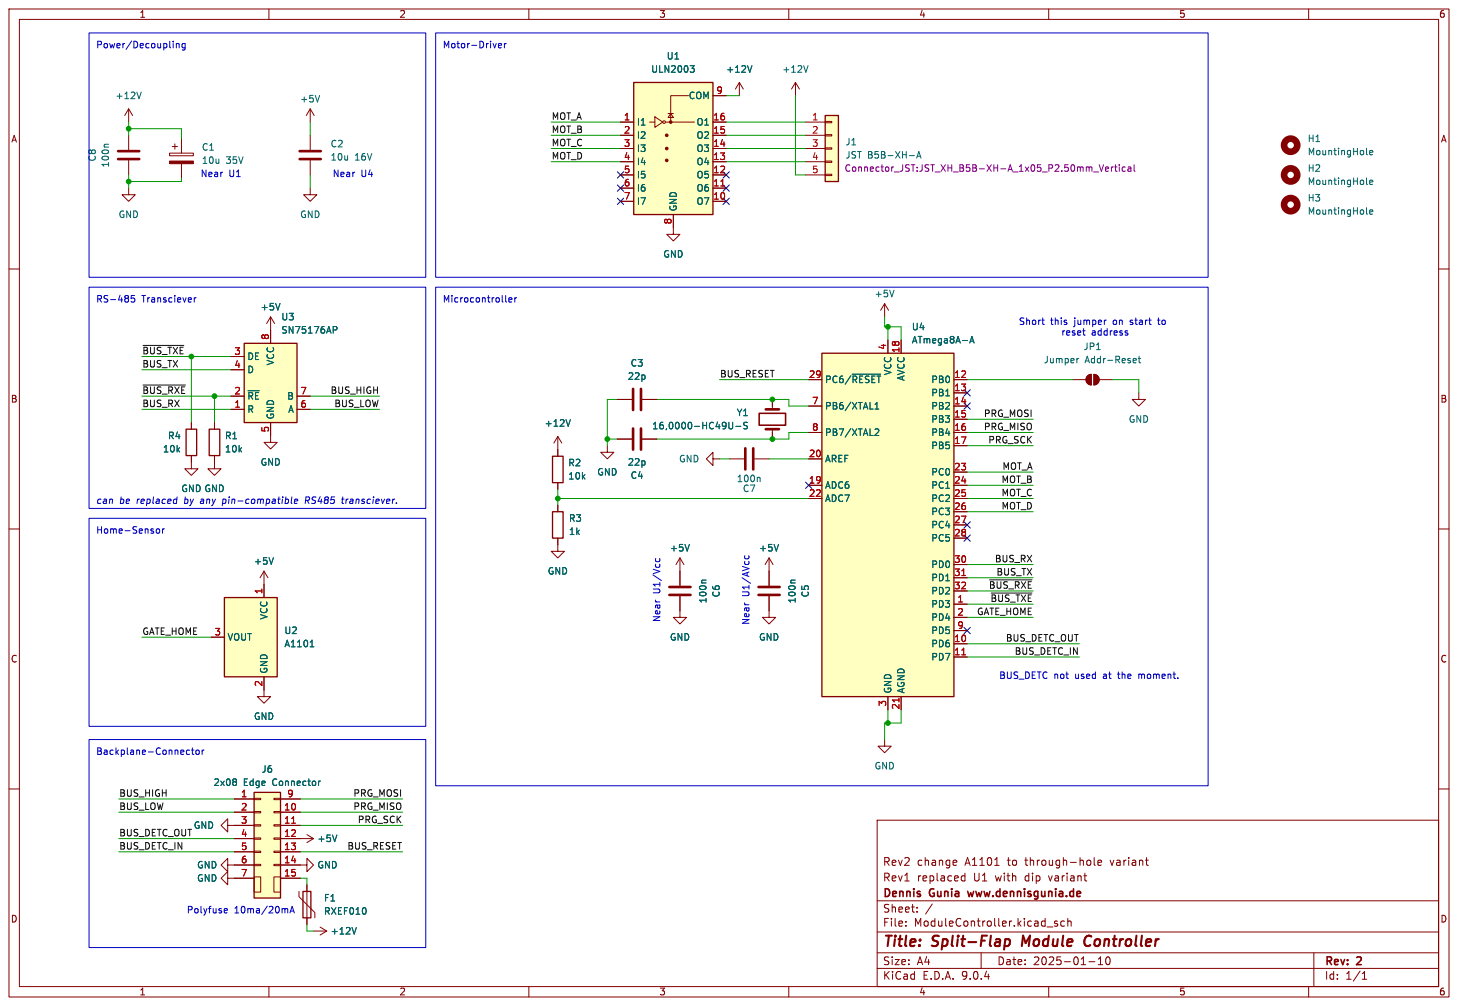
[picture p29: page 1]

JST B5B-XH-A Connector_JST:JST_XH_B5B-XH-A_1x05_P2.50mm_Vertical GND

reset address Near U1/Vcc
Jumper Addr-Reset GND

2x08 Edge Connector GND GND GND

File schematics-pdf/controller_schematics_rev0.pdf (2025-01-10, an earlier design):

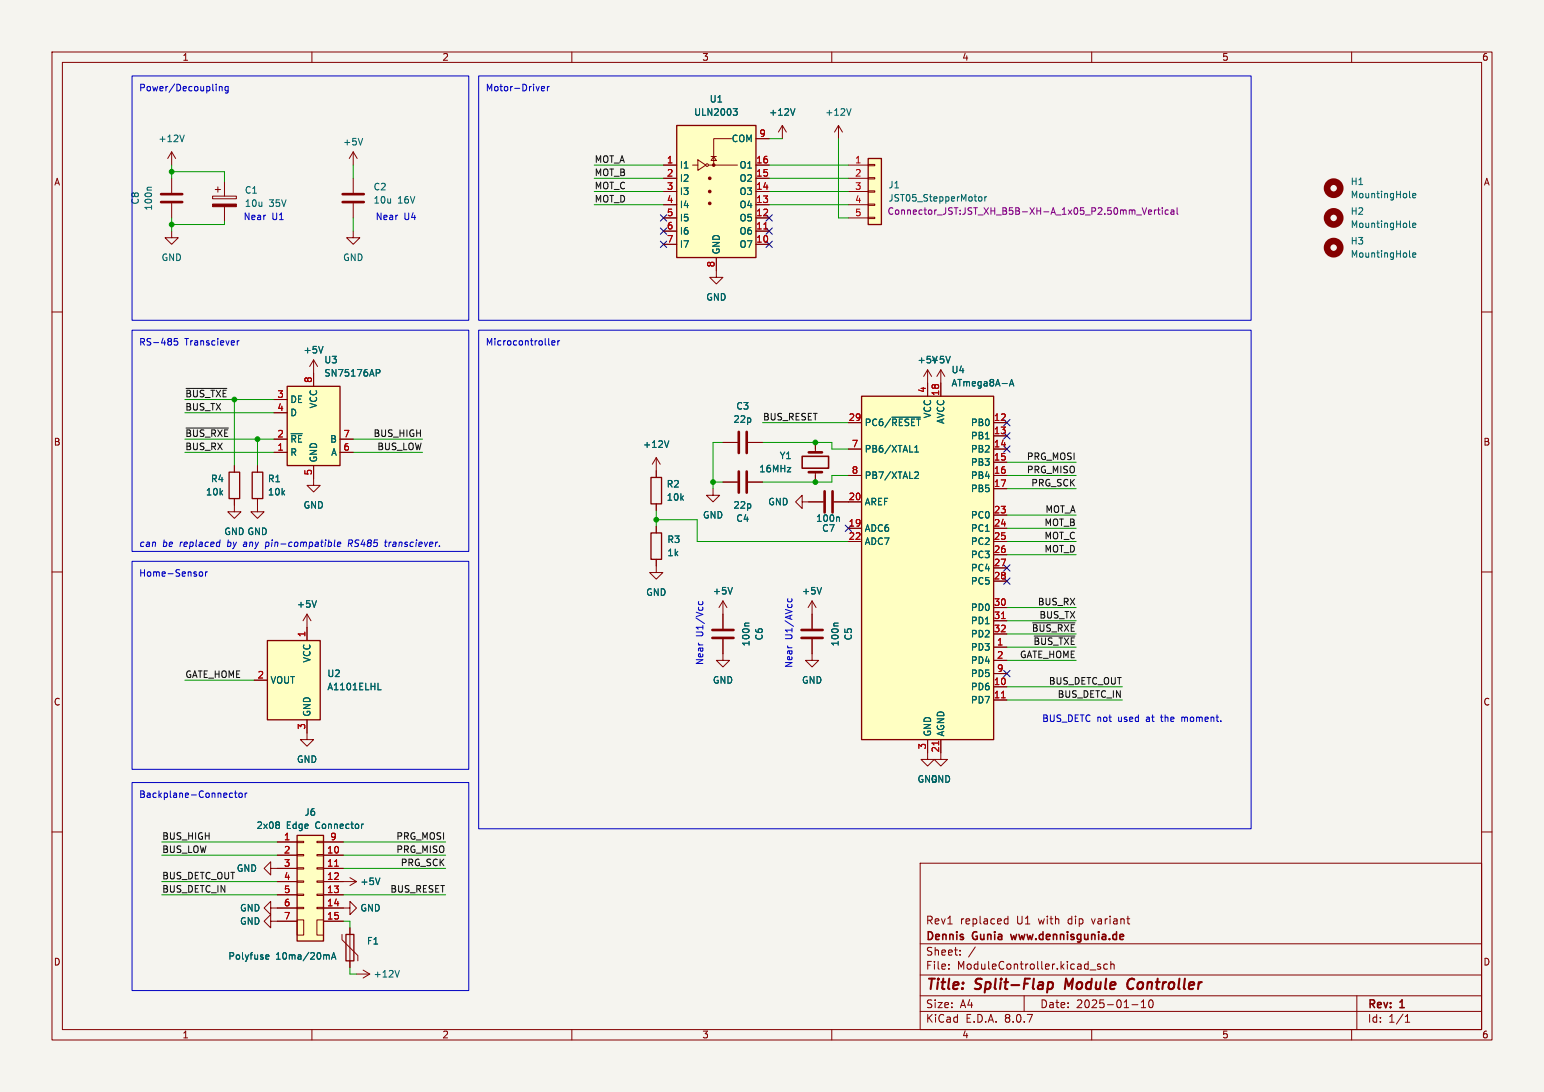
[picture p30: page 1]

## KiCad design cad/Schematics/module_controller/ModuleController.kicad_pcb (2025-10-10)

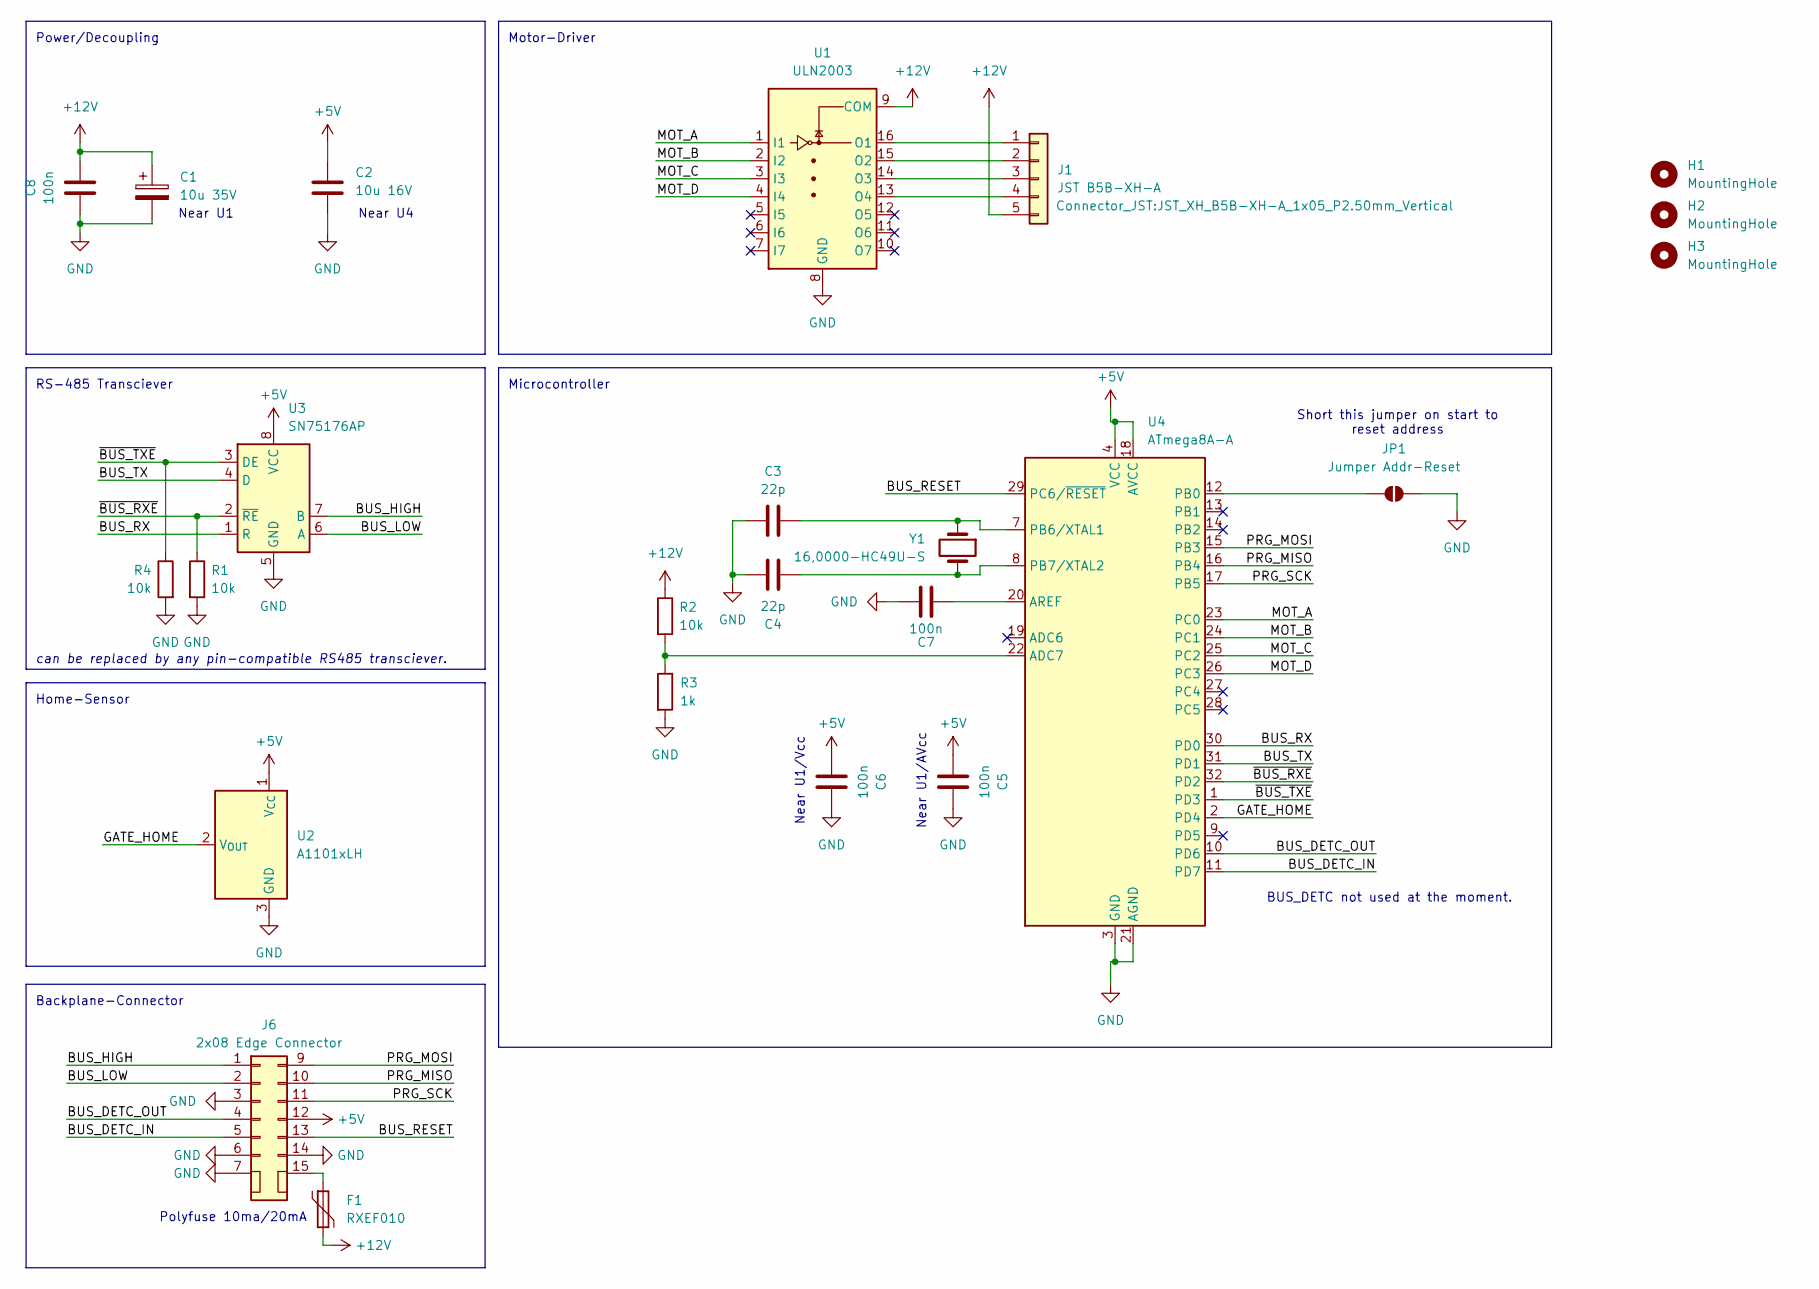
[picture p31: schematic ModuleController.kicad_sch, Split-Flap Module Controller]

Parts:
C1: 10u 35V; CP_Radial_D6.3mm_P2.50mm
C2: 10u 16V; C_1206_3216Metric
C3, C4: 22p; C_0805_2012Metric
C5, C6, C7, C8: 100n; C_0805_2012Metric
F1: RXEF010; Fuse_0805_2012Metric
H1, H2, H3: MountingHole; MountingHole_3.2mm_M3_DIN965_Pad
J1: JST B5B-XH-A; JST_XH_B5B-XH-A_1x05_P2.50mm_Vertical
J6: 2x08 Edge Connector; Card Edge 16 power
JP1: Jumper Addr-Reset; SolderJumper-2_P1.3mm_Open_Pad1.0x1.5mm
R1, R2, R4: 10k; R_0805_2012Metric
R3: 1k; R_0805_2012Metric
U1: ULN2003; DIP-16_W7.62mm
U2: A1101xLH; SOT-23W
U3: SN75176AP; DIP-8_W7.62mm
U4: ATmega8A-A; TQFP-32_7x7mm_P0.8mm
Y1: 16,0000-HC49U-S; Crystal_HC49-U_Vertical

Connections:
+5V: C2.1, C5.2, C6.2, J6.12, U2.1 (V_{CC}), U3.8 (VCC), U4.4 (VCC), U4.6 (VCC), U4.18 (AVCC)
+12V: C1.1, C8.1, F1.2, J1.5, R2.1, U1.9 (COM)
/BUS_DETC_IN: J6.5, U4.11 (PD7)
/BUS_DETC_OUT: J6.4, U4.10 (PD6)
/BUS_HIGH: J6.1, U3.7 (B)
/BUS_LOW: J6.2, U3.6 (A)
/BUS_RESET: J6.13, U4.29 (PC6/~RESET)
/BUS_RX: U3.1 (R), U4.30 (PD0)
/BUS_TX: U3.4 (D), U4.31 (PD1)
/GATE_HOME: U2.2 (V_{OUT}), U4.2 (PD4)
/MOT_A: U1.1 (I1), U4.23 (PC0)
/MOT_B: U1.2 (I2), U4.24 (PC1)
/MOT_C: U1.3 (I3), U4.25 (PC2)
/MOT_D: U1.4 (I4), U4.26 (PC3)
/PRG_MISO: J6.10, U4.16 (PB4)
/PRG_MOSI: J6.9, U4.15 (PB3)
/PRG_SCK: J6.11, U4.17 (PB5)
/~BUS_RXE: R1.1, U3.2 (~RE), U4.32 (PD2)
/~BUS_TXE: R4.1, U3.3 (DE), U4.1 (PD3)
GND: C1.2, C2.2, C3.1, C4.1, C5.1, C6.1, C7.1, C8.2, J6.3, J6.6, J6.7, J6.14, JP1.2 (B), R1.2, R3.2, R4.2, U1.8 (GND), U2.3 (GND), U3.5 (GND), U4.3 (GND), U4.5 (GND), U4.21 (AGND)
unnamed: J1.1, U1.16 (O1)
unnamed: J1.2, U1.15 (O2)
unnamed: J1.3, U1.14 (O3)
unnamed: J1.4, U1.13 (O4)
unnamed: F1.1, J6.15
unnamed: JP1.1 (A), U4.12 (PB0)
unnamed: R2.2, R3.1, U4.22 (ADC7)
unnamed: C7.2, U4.20 (AREF)
unnamed: C3.2, U4.7 (PB6/XTAL1), Y1.1
unnamed: C4.2, U4.8 (PB7/XTAL2), Y1.2

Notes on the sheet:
Motor-Driver
RS-485 Transciever
Power/Decoupling
Polyfuse 10ma/20mA
Home-Sensor
Short this jumper on start to reset address
Backplane-Connector
BUS_DETC not used at the moment.
Near U1
can be replaced by any pin-compatible RS485 transciever.
Near U1/AVcc
Near U1/Vcc
Microcontroller
Near U4

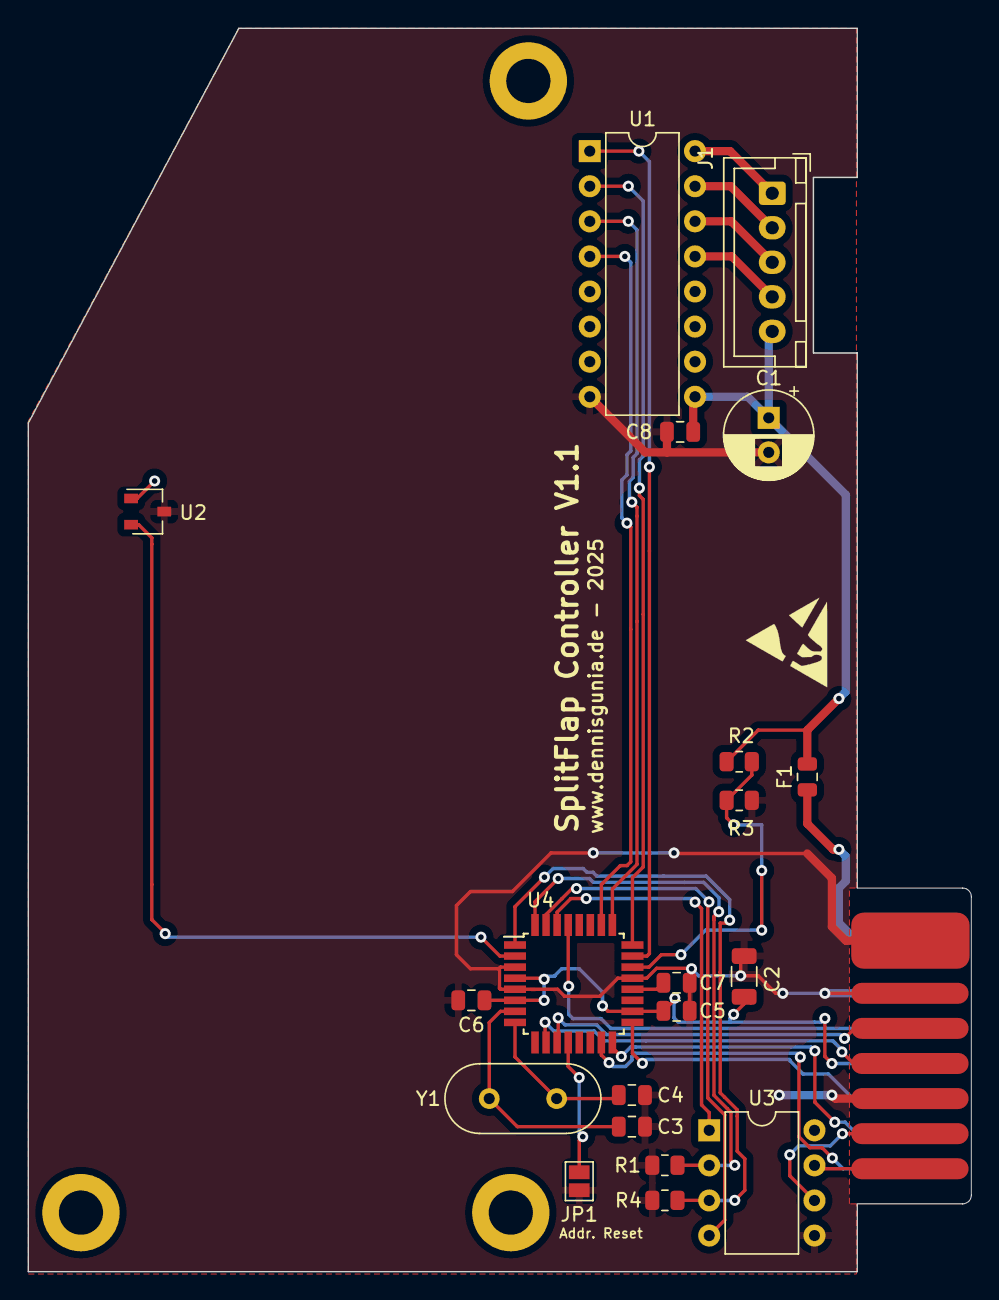
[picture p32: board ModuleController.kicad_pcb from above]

Board: 2 copper layers, 68.3 x 90.0 mm, 24 parts (0 on the bottom side), 30 nets.

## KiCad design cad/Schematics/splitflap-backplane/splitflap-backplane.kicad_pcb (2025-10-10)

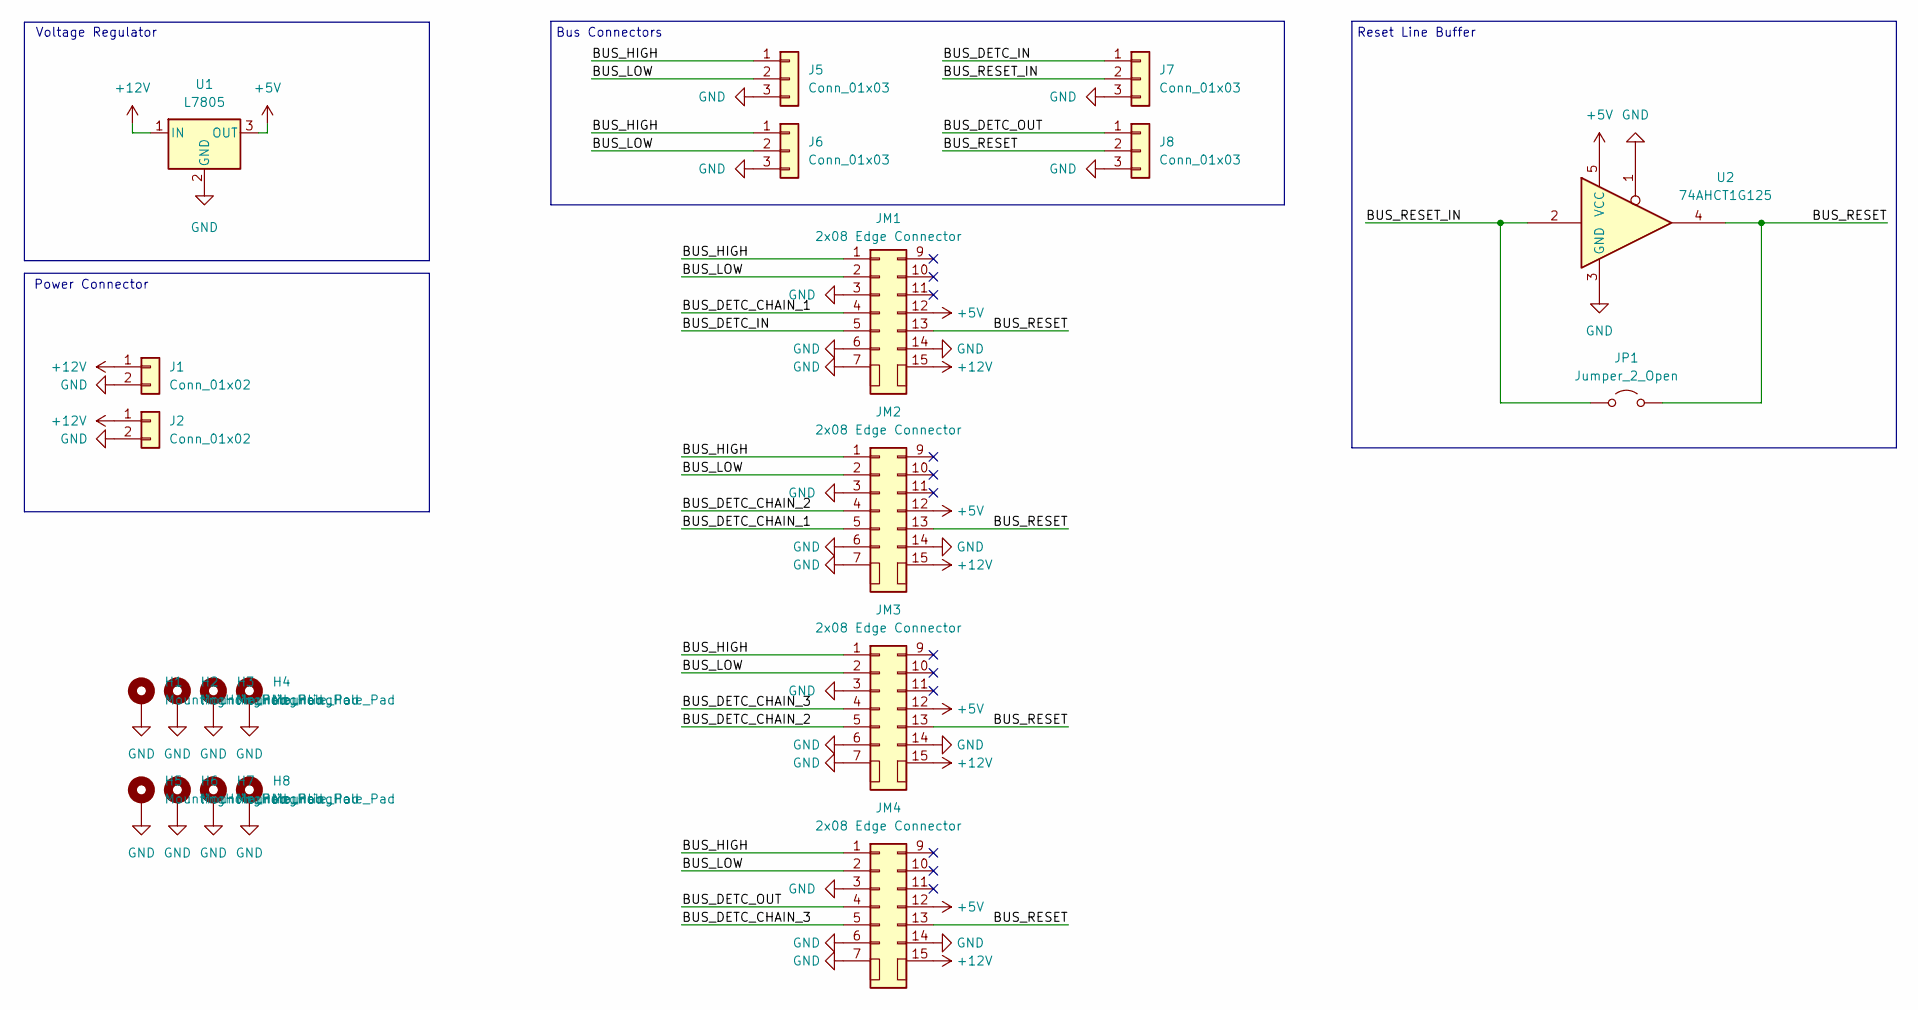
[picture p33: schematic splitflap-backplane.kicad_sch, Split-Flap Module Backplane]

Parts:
H1, H2, H3, H4, H5, H6, H7, H8: MountingHole_Pad; MountingHole_2.7mm_M2.5_DIN965_Pad
J1, J2: Conn_01x02; PhoenixContact_MSTBA_2,5_2-G-5,08_1x02_P5.08mm_Horizontal
J5, J6, J7, J8: Conn_01x03; PhoenixContact_MSTBA_2,5_3-G-5,08_1x03_P5.08mm_Horizontal
JM1, JM2, JM3, JM4: 2x08 Edge Connector; Card-Socket Flap Module
JP1: Jumper_2_Open; SolderJumper-2_P1.3mm_Open_Pad1.0x1.5mm
U1: L7805; TO-220-3_Horizontal_TabDown
U2: 74AHCT1G125; SOT-353_SC-70-5

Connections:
+5V: JM1.12, JM2.12, JM3.12, JM4.12, U1.3 (OUT), U2.5 (VCC)
+12V: J1.1, J2.1, JM1.15, JM2.15, JM3.15, JM4.15, U1.1 (IN)
/BUS_DETC_CHAIN_1: JM1.4, JM2.5
/BUS_DETC_CHAIN_2: JM2.4, JM3.5
/BUS_DETC_CHAIN_3: JM3.4, JM4.5
/BUS_DETC_IN: J7.1, JM1.5
/BUS_DETC_OUT: J8.1, JM4.4
/BUS_HIGH: J5.1, J6.1, JM1.1, JM2.1, JM3.1, JM4.1
/BUS_LOW: J5.2, J6.2, JM1.2, JM2.2, JM3.2, JM4.2
/BUS_RESET: J8.2, JM1.13, JM2.13, JM3.13, JM4.13, JP1.2 (B), U2.4
/BUS_RESET_IN: J7.2, JP1.1 (A), U2.2
GND: H1.1, H2.1, H3.1, H4.1, H5.1, H6.1, H7.1, H8.1, J1.2, J2.2, J5.3, J6.3, J7.3, J8.3, JM1.3, JM1.6, JM1.7, JM1.14, JM2.3, JM2.6, JM2.7, JM2.14, JM3.3, JM3.6, JM3.7, JM3.14, JM4.3, JM4.6, JM4.7, JM4.14, U1.2 (GND), U2.1, U2.3 (GND)

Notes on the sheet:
Voltage Regulator
Reset Line Buffer
Power Connector
Bus Connectors

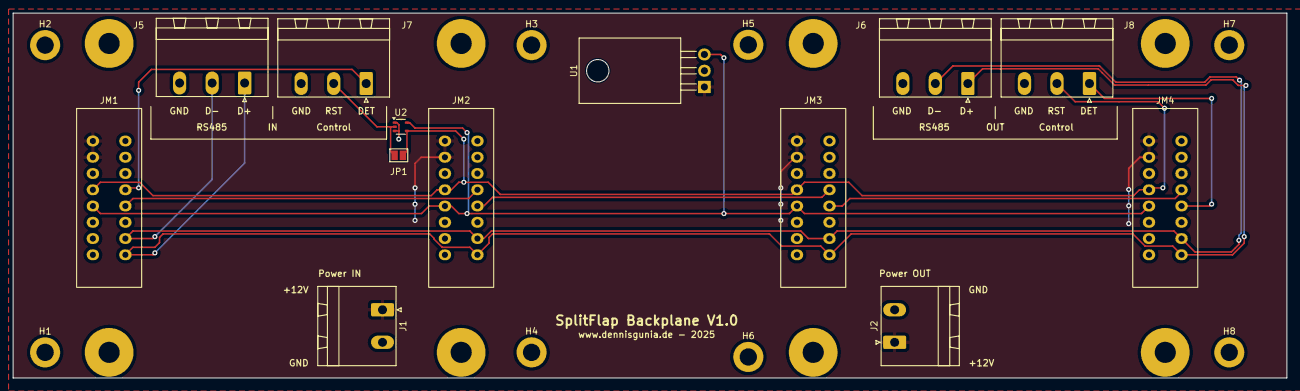
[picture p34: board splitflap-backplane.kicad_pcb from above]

Board: 2 copper layers, 199.0 x 57.0 mm, 21 parts (0 on the bottom side), 12 nets.

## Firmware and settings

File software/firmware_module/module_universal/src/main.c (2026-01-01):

/* Copyright (C) 2025 Dennis Gunia - All Rights Reserved
 * You may use, distribute and modify this code under the
 * terms of the  AGPL-3.0 license.
 *
 * https://www.dennisgunia.de
 * https://github.com/dennis9819/splitflap_v1
 */

#include "global.h"
#include "mctrl.h"
#include "rcount.h"
#include "rs485.h"

uint16_t address = 0x0000;
uint16_t calib_offset = 0x0000;
char *payload;


void eeprom_write_c(uint16_t address, uint8_t data)
{
    // disable interrupt
    cli();
    while (EECR & (1 << EEWE))
        ; // wait until previous write is done
    EEAR = address;
    EEDR = data;
    EECR |= (1 << EEMWE); // enable Master Write Enable
    EECR |= (1 << EEWE);  // write one
    sei();
}

uint8_t eeprom_read_c(uint16_t address)
{
    while (EECR & (1 << EEWE))
        ; // wait until previous write is done
    EEAR = address;
    EECR |= (1 << EERE); // read one
    return EEDR;
}

void initialSetup()
{
    wdt_disable();
    DDRB &= ~(1 << PB0); // Set PB0/JP1 as input
    PORTB |= (1 << PB0); // set pullup enable for PB0/JP1
    if (eeprom_read_c(CONF_ADDR_OKAY) == CONF_CONST_OKAY && (PINB && (1 << PB0)) > 0)
    {
        uint8_t addrL = eeprom_read_c(CONF_ADDR_ADDR);
        uint8_t addrH = eeprom_read_c(CONF_ADDR_ADDR + 1);
        address = addrL | (addrH << 8);
        uint8_t offsetL = eeprom_read_c(CONF_ADDR_OFFSET);
        uint8_t offsetH = eeprom_read_c(CONF_ADDR_OFFSET + 1);
        calib_offset = (offsetL | (offsetH << 8));
    }
    else
    {
        eeprom_write_c(CONF_ADDR_ADDR, (uint8_t)0x00);
        eeprom_write_c(CONF_ADDR_ADDR + 1, (uint8_t)0x00);
        eeprom_write_c(CONF_ADDR_OFFSET, (uint8_t)0x00);
        eeprom_write_c(CONF_ADDR_OFFSET + 1, (uint8_t)0x00);
        eeprom_write_c(CONF_ADDR_OKAY, CONF_CONST_OKAY);
    }
}
/* 
* Read and parse command from rx buffer
*/
void readCommand()
{
    char *payload_tmp = payload; // temporary pointer to payload buffer to avoid malloc/free every time
    int payload_len = parse_buffer(address, payload_tmp);
    if (payload_len > 0) // if positive, package is valid
    {
        payload_tmp += 2; // skip address bytes
        // read command byte
        uint8_t opcode = *payload_tmp;
        // parse commands
        if (opcode == CMDB_SETVAL)
        {
            // 0x1O = Set Digit
            uint8_t targetDigit = *(payload_tmp + 1);
            mctrl_set(targetDigit, 0);
        }
        else if (opcode == CMDB_SETVALR)
        {
            // 0x11 = Set Digit (full rotation)
            uint8_t targetDigit = *(payload_tmp + 1);
            mctrl_set(targetDigit, 1);
        }
        else if (opcode == CMDB_EEPROMR)
        {
            // 0xFO = READ EEPROM
            uint8_t bytes = 5;
            char *msg = malloc(bytes + 1);
            *msg = CMDR_ACK;
            for (uint16_t i = 1; i < (uint16_t)bytes + 1; i++)
            {
                *(msg + i) = (char)eeprom_read_c(i - 1);
            }
            _delay_ms(2);
            sfbus_send_frame_v2(0xFFFF, msg, bytes + 1);
            free(msg);
        }
        else if (opcode == CMDB_EEPROMW)
        {
            // 0xF1 = WRITE EEPROM
            eeprom_write_c(CONF_ADDR_OKAY, (char)0xFF);
            for (uint16_t i = 0; i < 4; i++)
            {
                eeprom_write_c(i, *(payload_tmp + 1 + i));
            }
            eeprom_write_c(CONF_ADDR_OKAY, CONF_CONST_OKAY);
            // respond with readout
            uint8_t bytes = 5;
            char *msg = malloc(bytes + 1);
            *msg = CMDR_ACK;
            for (uint16_t i = 1; i < (uint16_t)bytes + 1; i++)
            {
                *(msg + i) = (char)eeprom_read_c(i - 1);
            }
            _delay_ms(2);
            sfbus_send_frame_v2(0xFFFF, msg, bytes + 1);
            free(msg);
            // now use new addr
            uint8_t addrL = eeprom_read_c(CONF_ADDR_ADDR);
            uint8_t addrH = eeprom_read_c(CONF_ADDR_ADDR + 1);
            address = addrL | (addrH << SHIFT_1B);
        }
        else if (opcode == CMDB_GSTS)
        {
            char *msg = malloc(7);
            *msg = (char)getSts();
            uint16_t voltage = getVoltage();
            *(msg + 2) = (char)((voltage >> SHIFT_0B) & 0xFF);
            *(msg + 1) = (char)((voltage >> SHIFT_1B) & 0xFF);
            uint32_t counter = rc_getCounter();
            *(msg + 6) = (char)((counter >> SHIFT_0B) & 0xFF);
            *(msg + 5) = (char)((counter >> SHIFT_1B) & 0xFF);
            *(msg + 4) = (char)((counter >> SHIFT_2B) & 0xFF);
            *(msg + 3) = (char)((counter >> SHIFT_3B) & 0xFF);
            _delay_ms(2);
            sfbus_send_frame_v2(0xFFFF, msg, 7);
            free(msg);
        }
        else if (opcode == CMDB_GVER)
        {
            char *msg = malloc(3);
            *(msg + 0) = FVER_SEMVER_MAJOR;
            *(msg + 1) = FVER_SEMVER_MINOR;
            *(msg + 2) = FVER_SEMVER_PATCH;
            _delay_ms(2);
            sfbus_send_frame_v2(0xFFFF, msg, 3);
            free(msg);
        }
        else if (opcode == CMDB_PING)
        {
            char msg = (char)CMDR_PING;
            _delay_ms(2);
            sfbus_send_frame_v2(0xFFFF, &msg, 1);
        }
        else if (opcode == CMDB_RPWROFF)
        {
            mctrl_power(0);
        }
        else if (opcode == CMDB_PWRON)
        {
            mctrl_power(1);
        }
        else if (opcode == CMDB_RESET)
        {
            do
            {
                wdt_enable(WDTO_15MS);
                for (;;)
                {
                }
            } while (0);
        }
        else
        {
            // invalid opcode
            char msg = CMDR_ERR_INVALID;
            _delay_ms(2);
            sfbus_send_frame_v2(0xFFFF, &msg, 1);
        }
        //memset(payload_tmp, 0x00, PROTO_MAXPKGLEN); // clear buffer
    }
}

int main()
{
    payload = malloc(PROTO_MAXPKGLEN); // allocate payload buffer initially to avoid malloc/free every time
    initialSetup();
    rs485_init();
    setup_async_rx();
    mctrl_init(calib_offset);

    while (1 == 1)
    {
        readCommand();
    }
}

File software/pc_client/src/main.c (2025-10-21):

/*
 * This file is part of the split-flap project.
 * Copyright (c) 2024-2025 GuniaLabs (www.dennisgunia.de)
 * Authors: Dennis Gunia
 *
 * This program is licenced under AGPL-3.0 license.
 *
 */

#include <fcntl.h> // Contains file controls like O_RDWR
#include <stdio.h>
#include <stdlib.h>
#include <string.h>
#include <sys/ioctl.h>
#include <sys/types.h>
#include <termios.h> // Contains POSIX terminal control definitions
#include <unistd.h>  // write(), read(), close()

#include "console.h"
#include "devicemgr.h"
#include "logging/logger.h"
#include "serial/ftdi485.h"
#include "serial/sfbus.h"

extern char *optarg;

void printUsage(char *argv[])
{
    fprintf(stderr, "Usage: %s -p <tty> -c <command> [value]\n", argv[0]);
    exit(EXIT_FAILURE);
}

int main(int argc, char *argv[])
{

    // initialize logger
    init_logger(LOG_TRACE);
    log_message(LOG_INFO, "Starting split-flap pc client %s", "v1.0.0");
    log_message(LOG_INFO, "(c) 2024-2025 GuniaLabs (www.dennisgunia.de)");

    // parse arguments
    int opt = ' ';
    char *port = NULL, *config_file = NULL, *log_level = NULL;

    while ((opt = getopt(argc, argv, "p:c:l:")) != -1) // check options
    {
        switch (opt)
        {
        case 'p':
            port = optarg;
            break;
        case 'c':
            config_file = optarg;
            break;
        case 'l':
            log_level = optarg;
            break;
        default:
            printUsage(argv);
        }
    }


    if (log_level != NULL) // if log level specified
    {
        if (strlen(log_level) > 0)
        {                                                     // if log level specified
            long inputLogLevel = strtol(log_level, NULL, 10); // parse log level
            init_logger(inputLogLevel);                       // re-init logger with new level
        }
    }

    if (config_file == NULL) // if config file not specified
    {
        log_message(LOG_CRITICAL, "Please specify config file\n");
        printUsage(argv);
    }
    else
    {
        if (strlen(config_file) == 0) // if config file path empty
        {
            log_message(LOG_CRITICAL, "Please specify config file\n");
        }
        else
        {
            if (access(config_file, F_OK) != 0) // check if config file exists and can be opened
            {
                log_message(LOG_CRITICAL, "Config file: %s does not exist or cannot be opened\n", config_file);
                printUsage(argv);
            }
            else
            {
                log_message(LOG_INFO, "Use device configuration at '%s'", config_file);
            }
        }
    }

    if (port == NULL) // if port not specified
    {
        log_message(LOG_CRITICAL, "Please specify serial port\n");
        printUsage(argv);
    }
    else
    {
        if (strlen(port) == 0) // if port path empty
        {
            log_message(LOG_CRITICAL, "Please specify serial port\n");
            printUsage(argv);
        }
        else
        {
            if (access(port, F_OK) != 0) // check if port exists and can be opened
            {
                log_message(LOG_CRITICAL, "Serial port: %s does not exist or cannot be opened\n", port);
                printUsage(argv);
            }
            else
            {
                log_message(LOG_INFO, "Use serial port at '%s'", port);
            }
        }
    }

    int fd = rs485_init(port, B57600); // setup rs485
    devicemgr_init(fd);                // init device manager
    devicemgr_load(config_file);       // load config file on startup
    start_console(fd, config_file);    // start console
    return 0;
}

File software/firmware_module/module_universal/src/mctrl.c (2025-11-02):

/* Copyright (C) 2025 Dennis Gunia - All Rights Reserved
 * You may use, distribute and modify this code under the
 * terms of the  AGPL-3.0 license.
 *
 * https://www.dennisgunia.de
 * https://github.com/dennis9819/splitflap_v1
 */


#include "mctrl.h"

// Motor driver steps definition. Reverse for direction change.
#if MOTOR_DIR == 1
uint8_t motor_steps[4] = {
    0b00001000,
    0b00000100,
    0b00000010,
    0b00000001,
};
#elif MOTOR_DIR == 0
uint8_t motor_steps[4] = {
    0b00000001,
    0b00000010,
    0b00000100,
    0b00001000,
};
#endif

uint8_t step_index = 0;        // current index in motor_steps
uint8_t target_flap = 0;       // target flap
uint16_t absolute_pos = 0;     // absolute position in steps
uint16_t steps_since_home = 0; // steps since last home signal

// homing util variables
uint8_t homing = 0;   // current homing step
uint8_t lastSens = 0; // home sonsor signal from last tick

// counter for auto powersaving
uint16_t ticksSinceMove = 0;

// value to goto after the current is reached. 255 = NONE.
uint8_t afterRotation = STEPS_AFTERROT;

int16_t *delta_err;

// error and status flags
uint8_t sts_flag_errorTooBig = 0; // last home signal too early or too late
uint8_t sts_flag_noHome = 0;      // no home signal detected. Wheel stuck
uint8_t sts_flag_fuse = 0;        // blown fuse detcted
uint8_t sts_flag_pwrdwn = 0;      // device is powered down by controller
uint8_t sts_flag_failsafe = 0;    // device is powered down for safety reasons
uint8_t sts_flag_busy = 0;        // device is busy
// voltage monitoring variables
uint16_t currentVoltage = 0;      // current ADC reading
uint8_t currentFaultReadings = 0; // ticks with faulty readings (too many will
                                  // trip pwrdwn and sts_flag_fuse)
uint16_t timer_ticks = 0;

int STEPS_OFFSET = 0;
// initialize motor controller
void mctrl_init(int cal_offset)
{
    if (cal_offset < 800)
    {
        STEPS_OFFSET = STEPS_OFFSET_DEF;
    }
    else
    {
        STEPS_OFFSET = cal_offset;
    }
    DDRC = 0x0F;  // set all pins as outputs
    PORTC = 0x00; // set all to LOW

    DDRD &= ~(1 << PIN_SENSE); // PIN_SENSE is input
    PORTD |= (1 << PIN_SENSE); // PIN_SENSE pullup

    // setup adc
    ADMUX = 0xC7;                                      // Internal Vref at 2.56V, ADC7
    ADCSRA = (1 << ADEN) | (1 << ADSC) | (1 << ADPS1); // Enable ADC, Start first
                                                       // reading No freerunning, 8MHz
    while ((ADCSRA & (1 << ADSC)) > 0)
    {
    };
    // wait until first reading is complete,
    // to avoid error flag on first tick!

    // setup timer for ISR
    TCCR1A = 0;
    TCCR1B = (1 << WGM12) | (1 << CS11) | (1 << CS10); // CTC und Prescaler 64 (CLK=250kHz)
    OCR1A = MISR_OCR1A;                                // Equals roughly 431Hz (23.2ms Intervall)
    TIMSK = 1 << OCIE1A;                               // Timerinterrupts aktivieren
    homing = 1;
    delta_err = malloc(ERROR_DATASETS * sizeof(uint16_t));
    _delay_ms(MDELAY_STARTUP);
    sei();
}

// call when critical fail. Powers down motor and sets flags
void failSafe()
{
    sts_flag_failsafe = 1;
    PORTC = 0x00;
}

// read voltage non blocking (called every tick)
void readVoltage()
{
    currentVoltage = ADC;  // read last measurement
    ADMUX = 0xC7;          // select ADC7
    ADCSRA |= (1 << ADSC); // trigger next reading
    if (currentVoltage < MVOLTAGE_LSTOP)
    { // if voltage is too low, fuse is probably broken
        currentFaultReadings++;
        if (currentFaultReadings > MVOLTAGE_FAULTRD)
        { // too many fault readings trigger failSafe
            sts_flag_fuse = 1;
            failSafe();
        }
    }
}
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

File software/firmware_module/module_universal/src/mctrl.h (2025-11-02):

/* Copyright (C) 2025 Dennis Gunia - All Rights Reserved
 * You may use, distribute and modify this code under the
 * terms of the  AGPL-3.0 license.
 *
 * https://www.dennisgunia.de
 * https://github.com/dennis9819/splitflap_v1
 */


#include "global.h"
#include "rcount.h"

#pragma once

#define STEPS_PER_REV 2025    // steps per revolution
#define STEPS_PER_FLAP 45     // steps per flap
#define STEPS_ADJ 0           // added per flap to compensate for motor power down
#define STEPS_OFFSET_DEF 1400 // ansolute offset between home and first flap
#define AMOUNTFLAPS 45        // amount of flaps installed in system
#define STEPS_AFTERROT 255    // value to goto after current target flap is reached
#define ERROR_DATASETS 8      // length of error array

#define MDELAY_STARTUP 1000   // delay to wait after motor startup
#define MHOME_TOLERANCE 1.5   // tolerance for intial homing procedure
#define MHOME_ERRDELTA 30     // maximum deviation between expected home and actual home
#define MVOLTAGE_FAULTRD 20   // max. amount of fault readings before flag is set
#define MVOLTAGE_LSTOP 128    // lower voltage threshold for fuse detection
#define MPWRSVG_TICKSTOP 4310 // inactive ticks before motor shutdown (4310 ~ 10s)

#define MISR_OCR1A 580 // tick timer (defines rotation speed. euqals to ISR freq ~ 431Hz)
// 450, 480 also possible ?

#ifdef __cplusplus
extern "C"
{
#endif // __cplusplus
    void mctrl_init(int cal_offset);
    void mctrl_step();
    void mctrl_set(uint8_t flap, uint8_t fullRotation);

    void getErr(int16_t *error);
    uint8_t getSts();
    uint16_t getVoltage();
    void mctrl_power(uint8_t state);

    uint16_t timer_ticks;
#ifdef __cplusplus
}
#endif // __cplusplus

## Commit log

2025-01-10 Added fuse settings to makefile
2025-01-10 refactor v1
    [Module.step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]
2025-01-10 added kicad generation script
2025-01-10 Refactor schematics
    [ModuleController.kicad_sch]
2025-02-21 improved formatting and fixed clangd includes
    [global.h, main.c, mctrl.c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]
2025-02-21 fix clangd and comments
    [global.h, mctrl.c, mctrl.h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]
2025-09-11 update schematics
    [bass od 1r1.kicad_sch, splitflap-backplane.kicad_pcb, splitflap-backplane.kicad_sch]
2025-09-12 fix controller for ftdi485
    [main.c]
2025-09-12 fix calibration
2025-09-18 updated schematics
    [ModuleController.kicad_pcb, ModuleController.kicad_sch]
2025-10-10 refactor, add cad
    [Module.step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]
2025-10-12 Add BOM
2025-10-12 Fix BOM
2025-10-19 fix protocol V2 bug
    [main.c, rs458.c]
2025-10-19 fix stl files
    [splitflap-drum-outer-1u.stl, splitflap-drum-outer-2u.stl]
2025-10-19 add power section to doc
2025-10-20 fix includes and type
    [main.c]
2025-10-21 fix segfault on load
    [main.c]
2025-10-22 added firmware for new pcb revision
2025-10-22 patch voltage readout for new firmware version
2025-11-01 fix sense pin
2025-11-01 fix address form and calibration form
2025-11-01 add print profiles and update schematics
    [ModuleController.kicad_sch, SF_Flaps_V1.3mf]
2025-11-02 fix print profile
    [SF_Flaps_V1.3mf]
2025-11-02 update schematics annotation
    [ModuleController.kicad_sch]
2025-11-02 fix motor standby and overheating issue
    [mctrl.c, mctrl.h]
2026-01-01 fixed buffer overflow in processing function and added documentation
    [main.c, rs458.c]
2026-01-01 update settings
    [SF_Flaps_V1.3mf]
